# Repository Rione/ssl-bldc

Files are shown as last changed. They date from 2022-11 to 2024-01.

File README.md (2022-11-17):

# Ri-one BLDC Driver V1

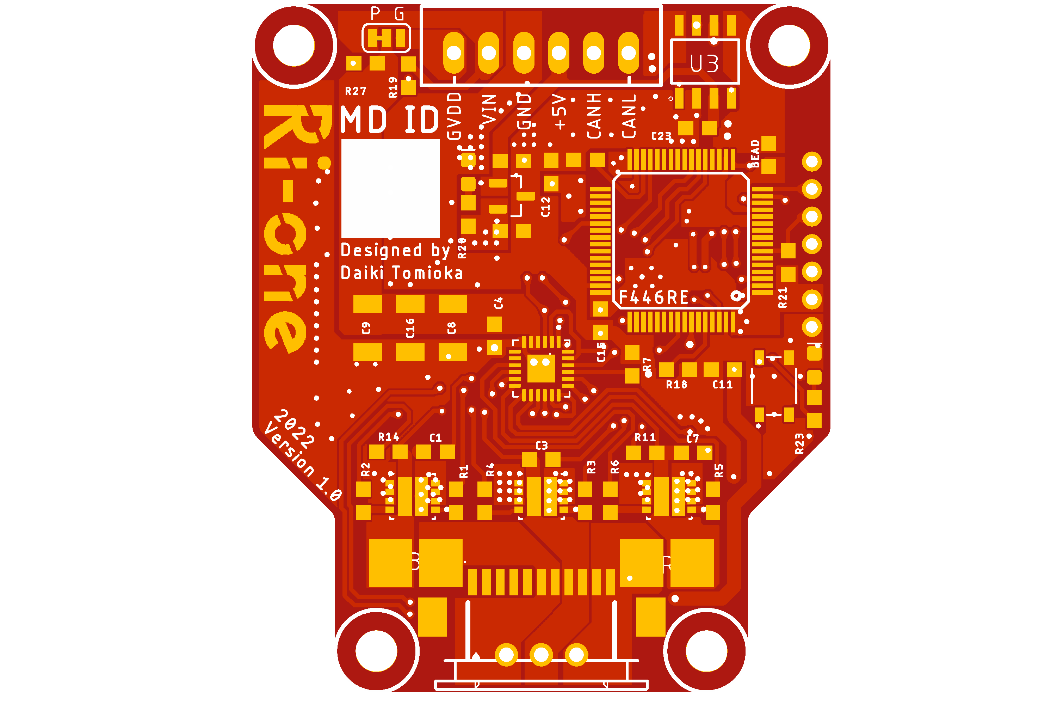
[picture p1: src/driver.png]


|  | IC |
| --- | --- |
| MOSFET | [SIZ254DT-T1-GE3](https://www.mouser.jp/ProductDetail/Vishay-Siliconix/SIZ254DT-T1-GE3?qs=pUKx8fyJudCKVjpWQE2G2A%3D%3D) |
| MCU | [STM32F446RET6](https://jp.rs-online.com/web/p/microcontrollers/1106621) |
| Gate Driver | [DVR8300DRGER](https://www.ti.com/product/DRV8300/part-details/DRV8300DRGER) |
| CAN Transceiver | [TJA1441AT](https://akizukidenshi.com/catalog/g/gI-17464/) |
| Shunt Resistor| 10mΩ | 
| 3.3V Regulator | [AP7333-33SAG](https://akizukidenshi.com/catalog/g/gI-11360/) |
| Motor | [EC 45 flat 30W](https://www.maxongroup.com/medias/sys_master/root/8846629470238/20-JP-285.pdf)|

---

初めて作ったモータドライバ基板です．
記事も書いたので，良かったら見てください．
[tomixrm 初のモタドラ設計！！ゲート抵抗を計算して求めてみた](https://tomixrm.vercel.app/2e7cb67096e143f2a43334a63c00d47e)

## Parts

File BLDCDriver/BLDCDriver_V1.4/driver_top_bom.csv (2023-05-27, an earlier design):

Comment | Designator | Footprint | LCSC Part #
 | R10 R13 | SMS-REF
 | SJ1 SJ2 | SJ
MLB1608-470(f) | BEAD | 603
CC0603KRX7R9BB104 | C10 C18 | 1608
CC0603KRX7R9BB104 | C1 C3 C4 C7 C11 C12 C15 C23 C25 | 603
CR-03FL7----1K | R20 | R0603
CR-03FL7----1K | R23 | 603
YC124-JR-071KL | R24 | YC124-JR-071KL
4.7uF | C14 | 603
10k | R27 | R0603
10k | R18 | R0603
RMS06JT103 | R19 | 603
RMS06JT103 | R21 | R0603
CL31A226KAHNNNE | C8 C9 C16 C24 | 1210
CR0603FA51R0G | R1 R2 R3 R4 R5 R6 | 603
50k | R7 | 603
AP7333-33SAG-7 | REG | SOT95P237X112-3N
STM32F446RE | NUCLEO_MAIN | STM32F446RET6
FFC12_11PIN_1MM | . | CON-SMT-FFCFPC_52207-1185
XL-3528RGBW-HM | U$1 | 3528LSEKJ3ZGKQBKS
MCP2562-E/SN | U3 | SOIC127P600X175-8N
DRV8300DRGER | U1 | QFN50P400X400X100-25N
SIZ240DT-T1-GE3 | Q2 Q3 Q4 | TRANS_SIZ240DT-T1-GE3
SKRPACE010 | S1 | SW_SKRPACE010
WHITE | D3 D6 | LED-0603

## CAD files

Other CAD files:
BLDCDriver/BLDCDriver_V1.4/drive.dxf

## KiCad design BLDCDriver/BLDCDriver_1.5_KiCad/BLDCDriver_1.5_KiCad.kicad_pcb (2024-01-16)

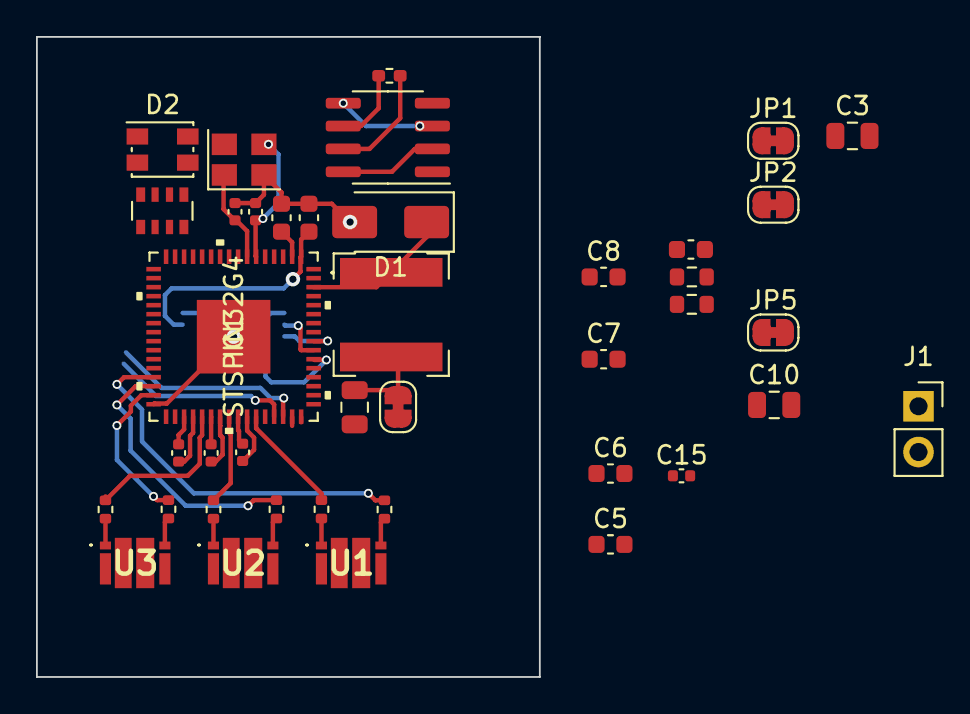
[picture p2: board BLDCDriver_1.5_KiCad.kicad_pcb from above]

Board: 2 copper layers, 27.9 x 35.6 mm, 41 parts (1 on the bottom side), 42 nets.

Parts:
C1, C2: 20p; C_0402_1005Metric
C3: 10uF; C_0805_2012Metric
C4, C6, C8, C9: 100nF; C_0603_1608Metric
C5, C7: 1uF; C_0603_1608Metric
C10: 220nF; C_0805_2012Metric
C11, C13, C14, C15: 1uF; C_0402_1005Metric
C12: N.M.; C_0603_1608Metric
C$1: 10uf 25v; C_0805_2012Metric
D1: SS210; D_SMA
D2: LED_RGBA; LED_Kingbright_AAA3528ESGCT
IC1: STSPIN32G4
J1: Conn_01x02_Male; PinSocket_1x02_P2.54mm_Vertical
JP1, JP2, JP3, JP5: Jumper_2_Bridged; SolderJumper-2_P1.3mm_Bridged_RoundedPad1.0x1.5mm
L1: 18uh; L_Bourns-SRN6028
R1: 22k; R_0603_1608Metric
R2: 10k; R_0603_1608Metric
R3: 120; R_0402_1005Metric_Pad0.72x0.64mm_HandSolder
R4, R5, R6, R7, R8, R9: 22k; R_0402_1005Metric
RN1: 1k; R_Array_Convex_4x0603
U1, U2, U3: SIZ254DTT1GE3
U4: MCP2562-E-SN; SOIC-8_3.9x4.9mm_P1.27mm
U5: AS5048A-HTSP-500; AS5048A_SOP65P640X120-14N
Y1: 12Mhz; Crystal_SMD_3225-4Pin_3.2x2.5mm

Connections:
BOOT1: C11.2, IC1.41 (BOOT1)
BOOT2: C13.2, IC1.38 (BOOT2)
BOOT3: C14.2, IC1.35 (BOOT3)
CANH: R3.1, U4.7 (CANH)
CANL: R3.2, U4.6 (CANL)
CAN_RD: IC1.47 (PA11), U4.4 (RXD)
CAN_TD: IC1.48 (PA12), U4.1 (TXD)
GHS1: IC1.43 (GHS1), R4.1
GHS2: IC1.40 (GHS2), R6.1
GHS3: IC1.37 (GHS3), R8.1
GLS1: IC1.29 (GLS1), R5.1
GLS2: IC1.30 (GLS2), R7.1
GLS3: IC1.31 (GLS3), R9.1
GND: C1.2, C2.2, C3.2, C4.2, C5.2, C6.2, C7.2, C8.2, C9.2, C10.2, C12.2, C15.1, C$1.2, D1.2 (A), IC1.32 (PGND), IC1.65 (VSS), R2.2, U1.5 (S), U2.5 (S), U3.5 (S), U4.2 (VSS), U4.8 (STBY), U5.13 (GND), Y1.2, Y1.4
unnamed: D2.3 (BK), RN1.2 (R2.1)
unnamed: D2.2 (GK), RN1.3 (R3.1)
unnamed: D2.1 (RK), RN1.4 (R4.1)
unnamed: C1.1, IC1.6 (PF0), Y1.3
unnamed: C2.1, IC1.7 (PF1), Y1.1
unnamed: C10.1, IC1.61 (VM), JP5.1 (A)
unnamed: C$1.1, JP3.1 (A), L1.2
unnamed: R4.2, U1.2 (G1)
unnamed: R5.2, U1.4 (G2)
unnamed: R6.2, U2.2 (G1)
unnamed: R7.2, U2.4 (G2)
unnamed: R8.2, U3.2 (G1)
unnamed: R9.2, U3.4 (G2)
OUT1: C11.1, IC1.42 (OUT1), U1.3 (O)
OUT2: C13.1, IC1.39 (OUT2), U2.3 (O)
OUT3: C14.1, IC1.36 (OUT3), U3.3 (O)
SCREF: C12.1, IC1.52 (SCREF), J1.2, R1.2, R2.1
SPI1_MISO: IC1.55 (PB4), U5.3 (MISO)
SPI1_MOSI: IC1.56 (PB5), U5.4 (MOSI)
SPI1_SCK: IC1.54 (PB3), U5.2 (CLK)
SW: D1.1 (K), IC1.62 (SW), L1.1
VBAT: C9.1, IC1.2 (VBAT), JP2.2 (B)
VCC: IC1.63 (VCC), JP1.1 (A), JP3.2 (B)
VD: U1.1 (D), U2.1 (D), U3.1 (D)
VDD: C3.1, C4.1, C15.2, D2.4 (A), IC1.1 (REG3V3/VDD), J1.1, JP2.1 (A), R1.1, U4.3 (VDD), U4.5 (Vio), U5.12 (VDD3V)
VDDA: C5.1, C6.1, IC1.27 (VDDA)
VREF+: C7.1, C8.1, IC1.26 (VREF+)
VREGIN: IC1.64 (REGIN), JP1.2 (B)

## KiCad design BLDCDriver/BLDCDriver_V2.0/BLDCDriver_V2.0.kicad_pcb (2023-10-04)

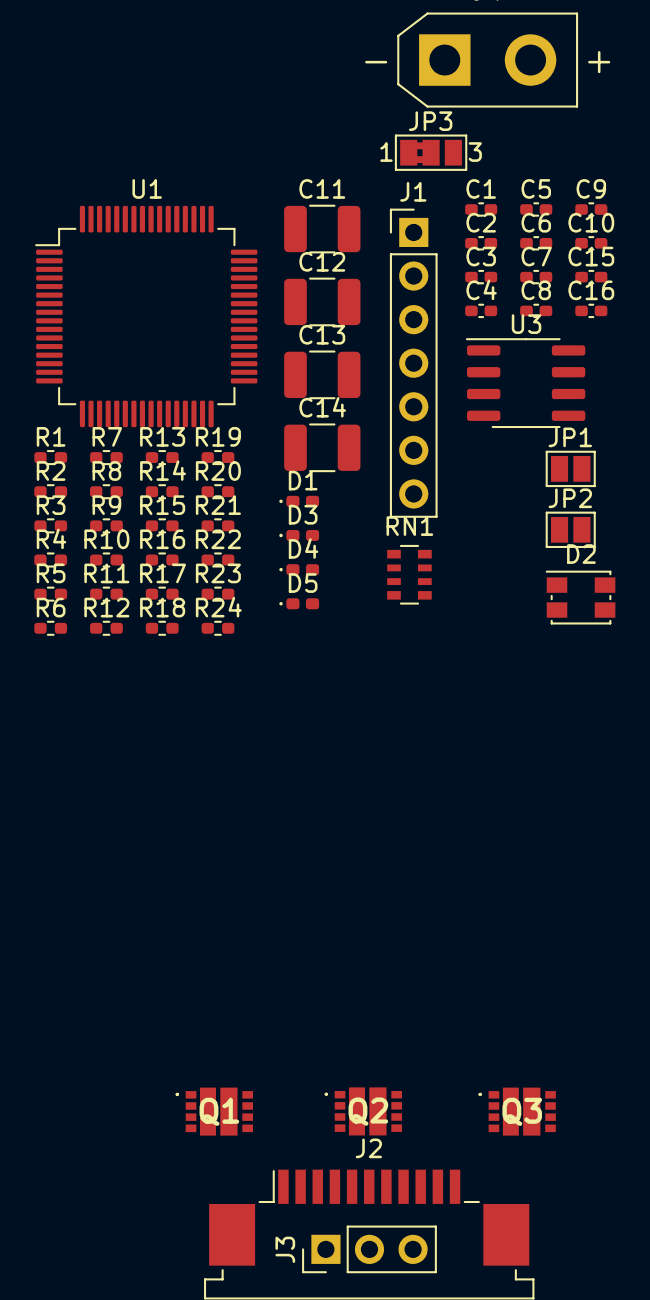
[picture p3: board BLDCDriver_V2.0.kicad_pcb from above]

Board: 2 copper layers, 58 parts (0 on the bottom side), 49 nets, no tracks yet.

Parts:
C1, C2, C3, C4, C5, C7, C8, C9, C10, C15, C16: 0.1u; C_0402_1005Metric_Pad0.74x0.62mm_HandSolder
C6: 4.7u; C_0402_1005Metric_Pad0.74x0.62mm_HandSolder
C11, C12, C13, C14: 22u; C_1210_3225Metric_Pad1.33x2.70mm_HandSolder
D1, D3, D4, D5: LED; LED_0402_1005Metric_Pad0.77x0.64mm_HandSolder
D2: LED_RGBA; LED_Kingbright_AAA3528ESGCT
J1: STLink; PinHeader_1x07_P2.54mm_Vertical
J2: Motor Out; TE_1-84952-1_1x11-1MP_P1.0mm_Horizontal
J3: Conn_01x03; PinHeader_1x03_P2.54mm_Vertical
J4: PowerIN; AMASS_XT30UPB-F_1x02_P5.0mm_Vertical
JP1, JP2: Jumper_2_Open; SolderJumper-2_P1.3mm_Open_Pad1.0x1.5mm
JP3: Jumper_3_Bridged12; SolderJumper-3_P1.3mm_Bridged2Bar12_Pad1.0x1.5mm_NumberLabe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
Q1, Q2, Q3: SIZ254DT-T1-GE3; SIZ254DTT1GE3
R1, R2, R15, R16: 10k; R_0402_1005Metric_Pad0.72x0.64mm_HandSolder
R3, R4, R5, R6, R7, R8, R9, R17: 1k; R_0402_1005Metric_Pad0.72x0.64mm_HandSolder
R10, R11, R12, R13: 33k; R_0402_1005Metric_Pad0.72x0.64mm_HandSolder
R14: 120; R_0402_1005Metric_Pad0.72x0.64mm_HandSolder
R18: 50k; R_0402_1005Metric_Pad0.72x0.64mm_HandSolder
R19, R20, R21, R22, R23, R24: 51; R_0402_1005Metric_Pad0.72x0.64mm_HandSolder
RN1: 1k; R_Array_Convex_4x0603
U1: (symbol "Device:C" (pin_numbers hide) (pin_names 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; LQFP-64_10x10mm_P0.5mm
U3: MCP2562-E-SN; SOIC-8_3.9x4.9mm_P1.27mm

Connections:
+3.3V: D2.4 (A), J1.1, U3.5 (Vio)
+3V3: C1.1, C2.1, C3.1, C4.1, C5.1, C7.1, C15.1, R1.1, R3.1
+5V: C16.1, U3.3 (VDD)
+BATT: C11.1, C12.1, C13.1, C14.1, J4.1, JP3.1 (A), Q1.2 (D), Q2.2 (D), Q3.2 (D), R15.1
CANH: R14.1, U3.7 (CANH)
CANL: R14.2, U3.6 (CANL)
CANRX: U1.62 (PB9), U3.4 (RXD)
CANTX: U1.61 (PB8), U3.1 (TXD)
GND: C6.2, C11.2, C12.2, C13.2, C14.2, C15.2, C16.2, D1.1 (K), D3.1 (K), D4.1 (K), D5.1 (K), J1.2, J2.MP (MountPin), J4.2, JP1.2 (B), JP2.2 (B), Q1.5 (S), Q2.5 (S), Q3.5 (S), R2.1, R10.2, R11.2, R18.2, U1.12 (VSSA), U1.18 (VSS), U1.31 (VSS), U1.47 (VSS), U1.63 (VSS), U3.2 (VSS), U3.8 (STBY)
LED: R17.1, U1.3 (PC14)
LED_B: RN1.7 (R2.2), U1.34 (PB13)
LED_G: RN1.6 (R3.2), U1.36 (PB15)
LED_R: RN1.5 (R4.2), U1.35 (PB14)
unnamed: C2.2, U1.19 (VDD)
unnamed: C3.2, U1.32 (VDD)
unnamed: C4.2, U1.48 (VDD)
unnamed: C5.2, U1.64 (VDD)
unnamed: D1.2 (A), R3.2
unnamed: D2.3 (BK), RN1.2 (R2.1)
unnamed: D2.2 (GK), RN1.3 (R3.1)
unnamed: D2.1 (RK), RN1.4 (R4.1)
unnamed: D3.2 (A), R15.2
unnamed: D4.2 (A), R16.2
unnamed: D5.2 (A), R17.2
unnamed: Q1.1 (G1), R19.2
unnamed: Q1.8 (G2), R20.2
unnamed: Q2.1 (G1), R21.2
unnamed: Q2.8 (G2), R22.2
unnamed: Q3.1 (G1), R23.2
unnamed: Q3.8 (G2), R24.2
unnamed: R2.2, U1.60 (BOOT0)
unnamed: R1.2, U1.7 (NRST)
unnamed: C1.2, U1.1 (VBAT)
unnamed: C6.1, U1.30 (VCAP_1)
unnamed: C7.2, U1.13 (VDDA)
unnamed: R6.2, R12.1
unnamed: R7.2, R10.1
unnamed: R8.2, R13.1
unnamed: R9.2, R11.1
U: C8.1, Q3.10 (O), R4.2, R6.1
UOut: J2.7, J2.8, J3.1, R4.1, R7.1
USBRX: J1.6, U1.17 (PA3)
V: C9.1, Q2.10 (O)
VDD: JP3.2 (C), JP3.3 (B), R16.1
VOut: J2.9, J2.10, J3.2
W: C10.1, Q1.10 (O), R5.2, R8.1
WOut: J2.11, J3.3, R5.1, R9.1
modeA: JP1.1 (A), U1.59 (PB7)
modeB: JP2.1 (A), U1.57 (PB5)

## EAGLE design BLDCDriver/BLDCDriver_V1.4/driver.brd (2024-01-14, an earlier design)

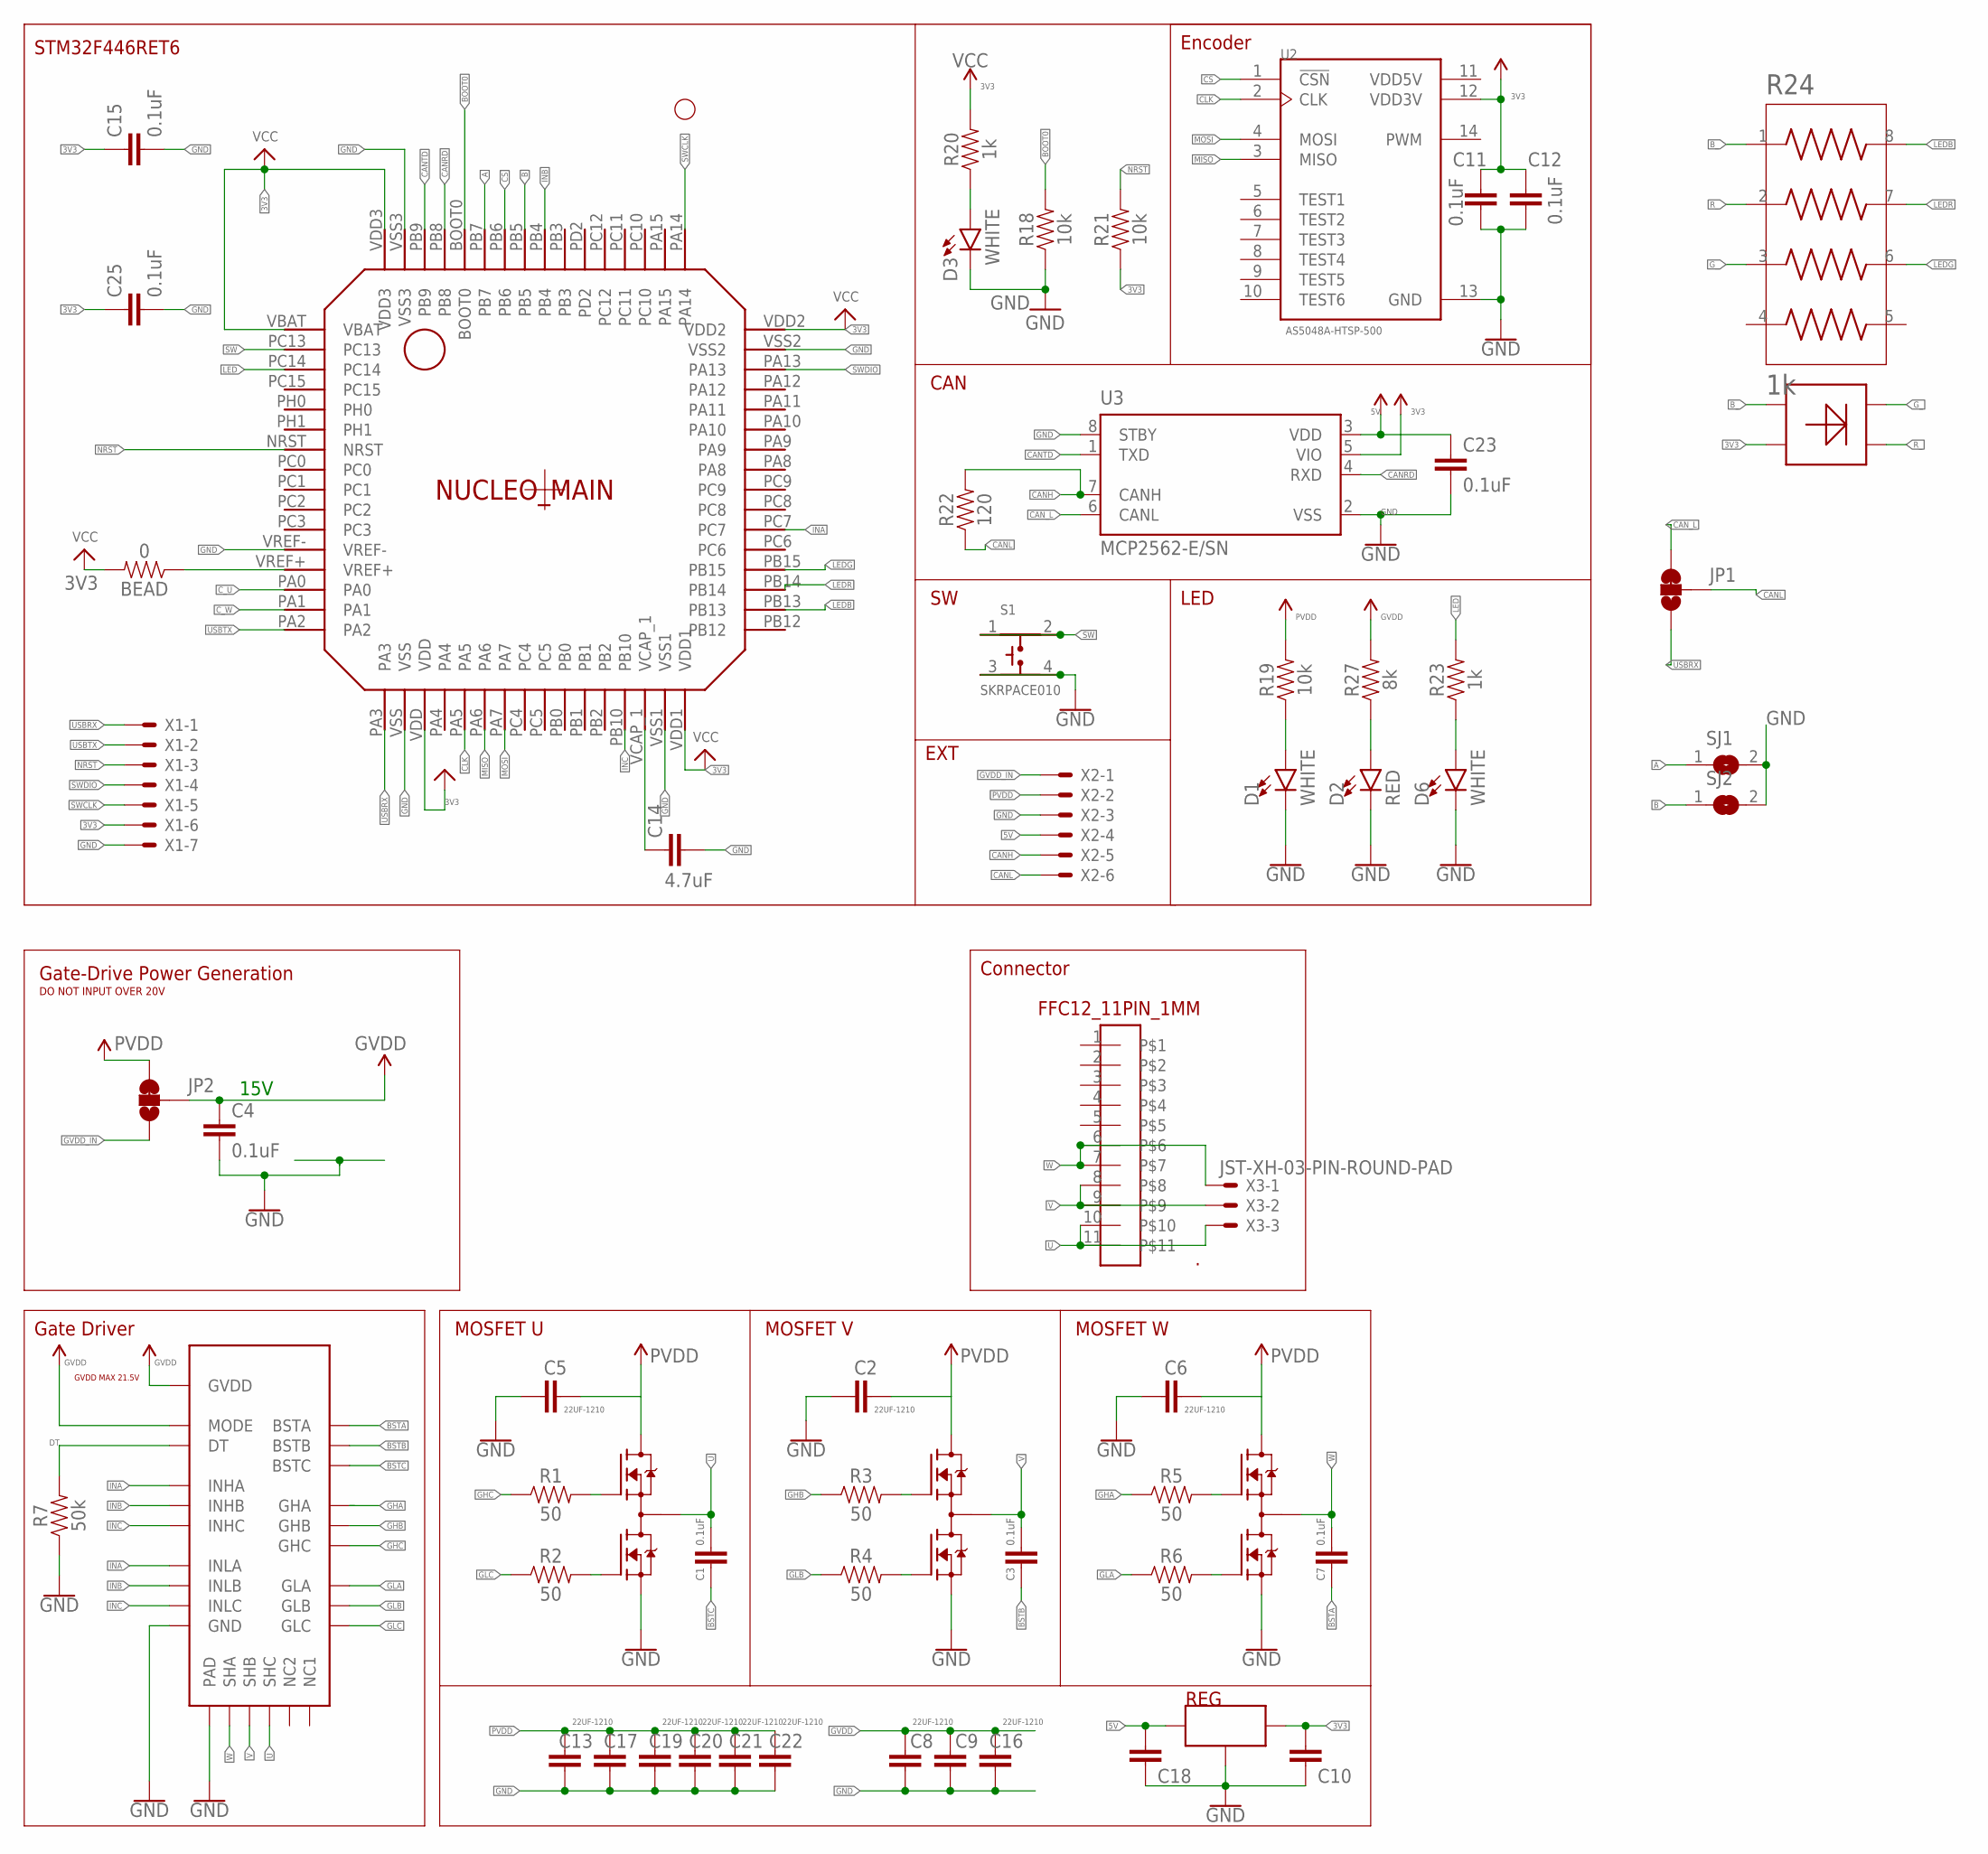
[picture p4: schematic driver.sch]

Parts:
.: FFC12_11PIN_1MM; CON-SMT-FFCFPC_52207-1185
BEAD: 0; 0603
C1, C3, C4, C7, C11, C12, C15, C23, C25: 0.1uF; 0603
C2, C5, C6, C8, C9, C13, C16, C17, C19, C20, C21, C22: 22UF-1210; 1210
C10, C18: 0.1UF; 1608
C14: 4.7uF; 0603
D1, D3, D6: WHITE; LED-0603
D2: RED; LED-0603
JP1, JP2: JUMPER-SMT_3_1-NC_TRACE_SILK; SMT-JUMPER_3_1-NC_TRACE_SILK
NUCLEO_MAIN: F446RET6; STM32F446RET6
Q2, Q3, Q4: SIZ240DT-T1-GE3; TRANS_SIZ240DT-T1-GE3
R1, R2, R3, R4, R5, R6: 50; 0603
R7: 50k; 0603
R18, R21: 10k; R0603
R19: 10k; 0603
R20: 1k; R0603
R22: 120; 0603
R23: 1k; 0603
R24: 1k; RESCAXS50P200X100X45-8N
R27: 8k; 0603
REG: AP7333; SOT95P237X112-3N
S1: SKRPACE010; SW_SKRPACE010
SJ1, SJ2: SJ
U1: QFN50P400X400X100-25NDRV8300DRGER; QFN50P400X400X100-25N
U2: AS5048A-HTSP-500; SOP65P640X120-14N
U3: MCP2562-E/SN; SOIC127P600X175-8N
U$1: LED; LED_AAA3528LSEKJ3ZGKQBKS
X1: JST-XH-07-PIN-ROUND-PAD; JST-XH-07-PACKAGE-ROUND-PAD
X2: JST-XH-06-PIN-LONG-PAD; JST-XH-06-PACKAGE-LONG-PAD
X3: JST-XH-03-PIN-ROUND-PAD; JST-XH-03-PACKAGE-ROUND-PAD

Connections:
3V3: BEAD.2, C10.1, C11.1, C12.1, C15.1, C25.1, NUCLEO_MAIN.VBAT, NUCLEO_MAIN.VDD, NUCLEO_MAIN.VDD1, NUCLEO_MAIN.VDD2, NUCLEO_MAIN.VDD3, R20.2, R21.1, REG.2 (OUT), U2.12 (VDD3V), U3.5 (VIO), U$1.4 (GND), X1.6
5V: C18.1, C23.1, REG.1 (IN), U3.3 (VDD), X2.4
A: NUCLEO_MAIN.PB7, SJ1.1
B: NUCLEO_MAIN.PB5, SJ2.1
BOOT0: NUCLEO_MAIN.BOOT0, R18.2
BSTA: C7.1, U1.BSTA
BSTB: C3.1, U1.BSTB
BSTC: C1.1, U1.BSTC
B_: R24.1, U$1.1 (B)
CANH: R22.2, U3.7 (CANH), X2.5
CANL: JP1.2, R22.1, X2.6
CANRD: NUCLEO_MAIN.PB8, U3.4 (RXD)
CANTD: NUCLEO_MAIN.PB9, U3.1 (TXD)
CAN_L: JP1.3, U3.6 (CANL)
CLK: NUCLEO_MAIN.PA5, U2.2 (CLK)
CS: NUCLEO_MAIN.PB6, U2.1 (!CSN)
C_U: NUCLEO_MAIN.PA0
C_W: NUCLEO_MAIN.PA1
DT: R7.2, U1.DT
GHA: R5.1, U1.GHA
GHB: R3.1, U1.GHB
GHC: R1.1, U1.GHC
GLA: R6.1, U1.GLA
GLB: R4.1, U1.GLB
GLC: R2.1, U1.GLC
GND: C2.1, C4.2, C5.1, C6.1, C8.1, C9.1, C10.2, C11.2, C12.2, C13.1, C14.2, C15.2, C16.1, C17.1, C18.2, C19.1, C20.1, C21.1, C22.1, C23.2, C25.2, D1.C, D2.C, D3.C, D6.C, NUCLEO_MAIN.VREF-, NUCLEO_MAIN.VSS, NUCLEO_MAIN.VSS1, NUCLEO_MAIN.VSS2, NUCLEO_MAIN.VSS3, Q2.5 (S2), Q2.6 (S2), Q2.7 (S2), Q3.5 (S2), Q3.6 (S2), Q3.7 (S2), Q4.5 (S2), Q4.6 (S2), Q4.7 (S2), R7.1, R18.1, REG.3 (GND), S1.3, S1.4, SJ1.2, SJ2.2, U1.GND, U1.PAD, U2.13 (GND), U3.2 (VSS), U3.8 (STBY), X1.7, X2.3
GVDD: C4.1, C8.2, C9.2, C16.2, JP2.2, R27.2, U1.GVDD, U1.MODE
GVDD_IN: JP2.1, X2.1
G_: R24.3, U$1.2 (G)
HA: Q4.1 (G1), R5.2
HB: Q3.1 (G1), R3.2
HC: Q2.1 (G1), R1.2
INA: NUCLEO_MAIN.PC7, U1.INHA, U1.INLA
INB: NUCLEO_MAIN.PB4, U1.INHB, U1.INLB
INC: NUCLEO_MAIN.PB10, U1.INHC, U1.INLC
L: D3.A, R20.1
LA: Q4.8 (G2), R6.2
LB: Q3.8 (G2), R4.2
LC: Q2.8 (G2), R2.2
LED: NUCLEO_MAIN.PC14, R23.2
LEDB: NUCLEO_MAIN.PB13, R24.8
LEDG: NUCLEO_MAIN.PB15, R24.6
LEDR: NUCLEO_MAIN.PB14, R24.7
MISO: NUCLEO_MAIN.PA6, U2.3 (MISO)
MOSI: NUCLEO_MAIN.PA7, U2.4 (MOSI)
unnamed: D1.A, R19.1
unnamed: D2.A, R27.1
unnamed: D6.A, R23.1
NRST: NUCLEO_MAIN.NRST, R21.2, X1.3
PVDD: C2.2, C5.2, C6.2, C13.2, C17.2, C19.2, C20.2, C21.2, C22.2, JP2.3, Q2.2 (D1), Q2.3 (D1), Q2.4 (D1), Q2.10 (D1), Q3.2 (D1), Q3.3 (D1), Q3.4 (D1), Q3.10 (D1), Q4.2 (D1), Q4.3 (D1), Q4.4 (D1), Q4.10 (D1), R19.2, X2.2
R_: R24.2, U$1.3 (R)
SW: NUCLEO_MAIN.PC13, S1.1, S1.2
SWCLK: NUCLEO_MAIN.PA14, X1.5
SWDIO: NUCLEO_MAIN.PA13, X1.4
U: ..10, ..11, C1.2, Q2.9 (S1/D2), U1.SHC, X3.3
USBRX: JP1.1, NUCLEO_MAIN.PA3, X1.1
USBTX: NUCLEO_MAIN.PA2, X1.2
V: ..8, ..9, C3.2, Q3.9 (S1/D2), U1.SHB, X3.2
VCAP: C14.1, NUCLEO_MAIN.VCAP_1
VDD5V: U2.11 (VDD5V)
VDDA: BEAD.1, NUCLEO_MAIN.VREF+
W: ..6, ..7, C7.2, Q4.9 (S1/D2), U1.SHA, X3.1

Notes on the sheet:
GVDD MAX 21.5V
15V
Gate-Drive Power Generation
Gate Driver
MOSFET U
Connector
Encoder
STM32F446RET6
MOSFET V
MOSFET W
DO NOT INPUT OVER 20V
CAN
LED
EXT

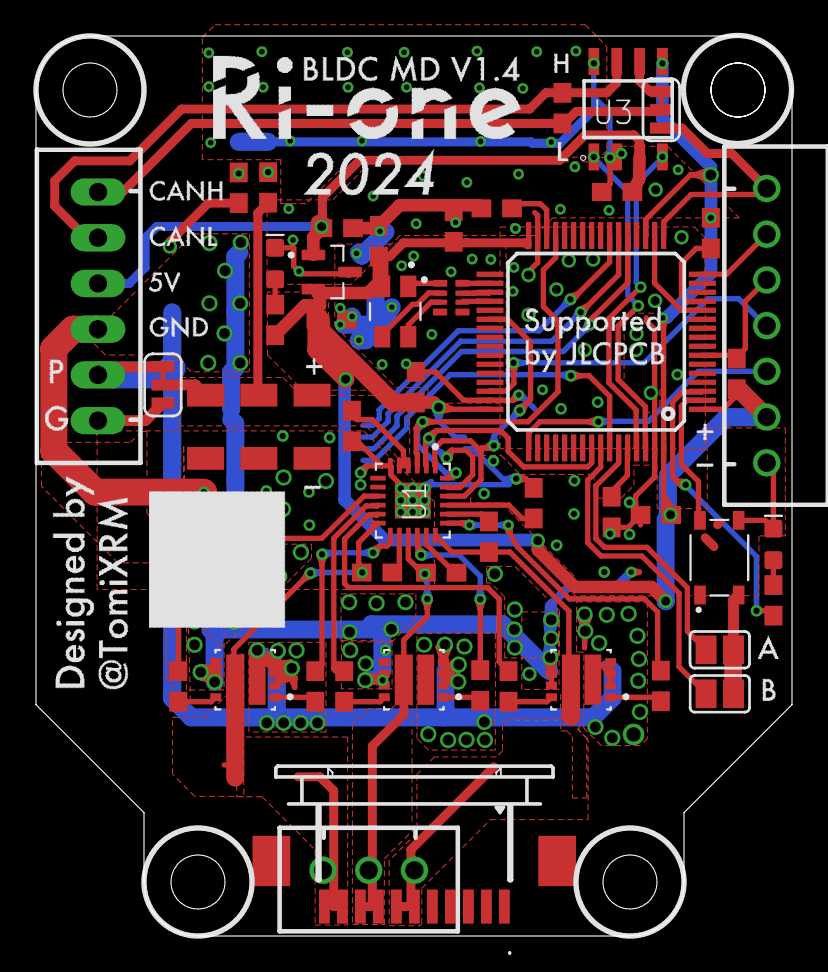
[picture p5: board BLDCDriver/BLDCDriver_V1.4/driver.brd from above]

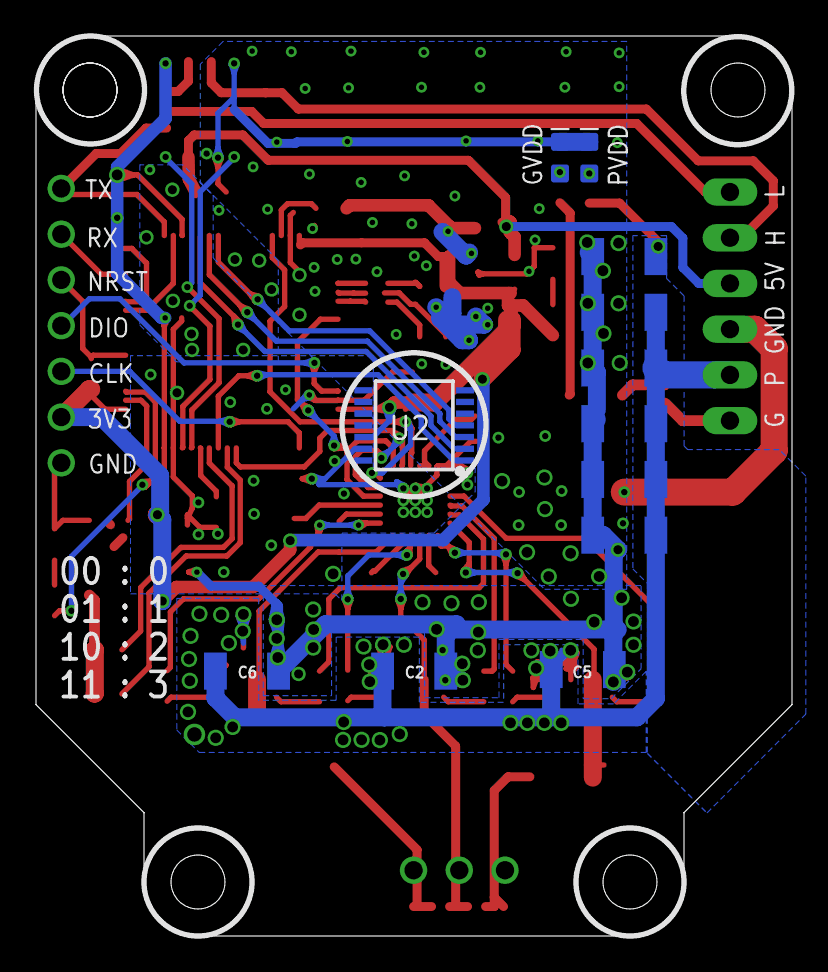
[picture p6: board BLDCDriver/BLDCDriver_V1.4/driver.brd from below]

Board: 2 copper layers, 42.0 x 50.0 mm, 62 parts (12 on the bottom side), 59 nets.

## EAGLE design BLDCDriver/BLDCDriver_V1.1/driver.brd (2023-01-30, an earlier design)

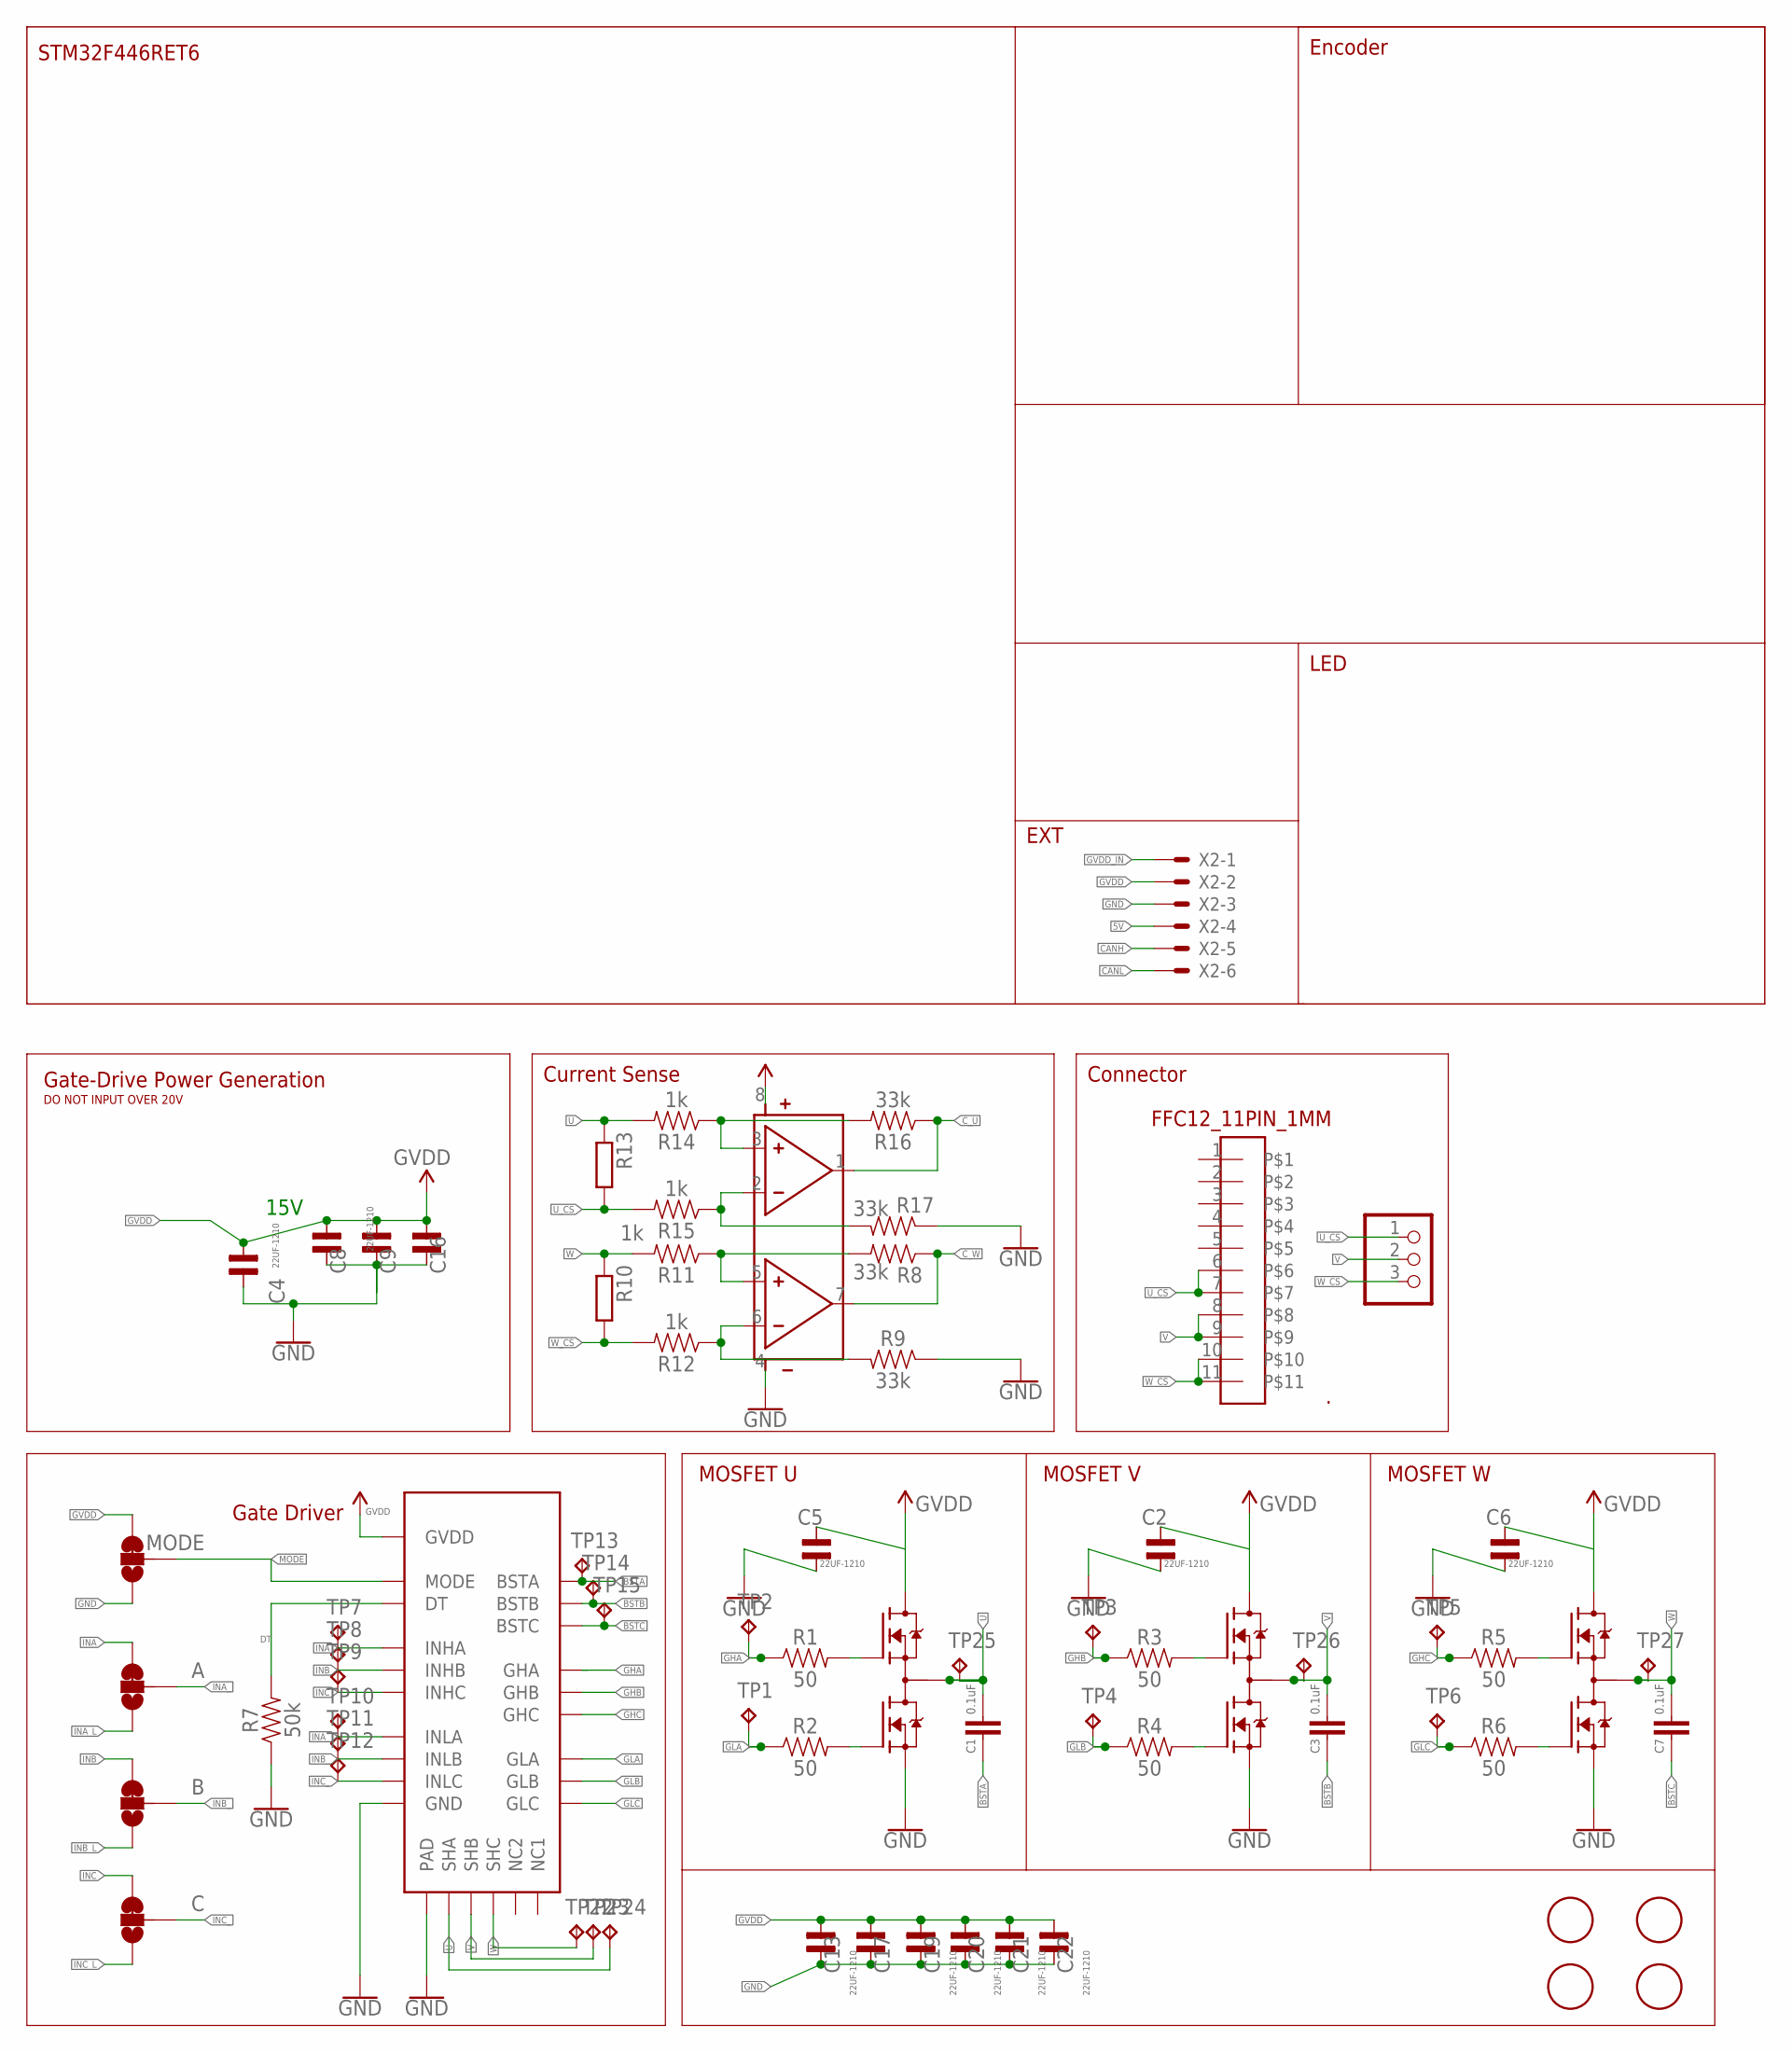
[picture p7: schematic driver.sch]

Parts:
.: FFC12_11PIN_1MM; CON-SMT-FFCFPC_52207-1185
A: JUMPER-SMT_3_1-NC_TRACE_SILK; SMT-JUMPER_3_1-NC_TRACE_SILK
B: JUMPER-SMT_3_1-NC_TRACE_SILK; SMT-JUMPER_3_1-NC_TRACE_SILK
C: JUMPER-SMT_3_1-NC_TRACE_SILK; SMT-JUMPER_3_1-NC_TRACE_SILK
C1, C3, C7: 0.1uF; 0603
C2, C5, C6, C8, C9, C13, C16, C17, C19, C20, C21, C22: 22UF-1210; 0805
C4: 0.1uF; 0805
JP3: PINHD-1X3CB; 1X03-CLEANBIG
MODE: JUMPER-SMT_3_1-NC_TRACE_SILK; SMT-JUMPER_3_1-NC_TRACE_SILK
Q2, Q3, Q4: SIZ240DT-T1-GE3; TRANS_SIZ240DT-T1-GE3
R1, R2, R3, R4, R5, R6: 50; 0603
R7: 50k; 0603
R8, R9, R16, R17: 33k; 0603
R10, R13: SMS-REF
R11, R12, R14, R15: 1k; 0603
TP1, TP2, TP3, TP4, TP5, TP6, TP7, TP8, TP9, TP10, TP11, TP12, TP13, TP14, TP15, TP22, TP23, TP24, TP25, TP26, TP27: TPPAD1-13; P1-13
U1: QFN50P400X400X100-25NDRV8300DRGER; QFN50P400X400X100-25N
U4: SOP80P620X125-8N
U$1, U$3, U$4, U$5: PIN; 3MM
X2: JST-XH-06-PIN-LONG-PAD; JST-XH-06-PACKAGE-LONG-PAD

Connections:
3V3: U4.8 (VDD)
5V: X2.4
BSTA: C1.1, TP13.TP, U1.BSTA
BSTB: C3.1, TP14.TP, U1.BSTB
BSTC: C7.1, TP15.TP, U1.BSTC
CANH: X2.5
CANL: X2.6
C_U: R16.1, U4.1 (O1)
C_W: R8.1, U4.7 (O2)
DT: R7.2, U1.DT
GHA: R1.1, TP2.TP, U1.GHA
GHB: R3.1, TP3.TP, U1.GHB
GHC: R5.1, TP5.TP, U1.GHC
GLA: R2.1, TP1.TP, U1.GLA
GLB: R4.1, TP4.TP, U1.GLB
GLC: R6.1, TP6.TP, U1.GLC
GND: C2.1, C4.2, C5.1, C6.1, C8.1, C9.1, C13.1, C16.1, C17.1, C19.1, C20.1, C21.1, C22.1, MODE.1, Q2.5 (S2), Q2.6 (S2), Q2.7 (S2), Q3.5 (S2), Q3.6 (S2), Q3.7 (S2), Q4.5 (S2), Q4.6 (S2), Q4.7 (S2), R7.1, R9.1, R17.1, U1.GND, U1.PAD, U4.4 (GND), X2.3
GVDD: C2.2, C4.1, C5.2, C6.2, C8.2, C9.2, C13.2, C16.2, C17.2, C19.2, C20.2, C21.2, C22.2, MODE.3, Q2.2 (D1), Q2.3 (D1), Q2.4 (D1), Q2.10 (D1), Q3.2 (D1), Q3.3 (D1), Q3.4 (D1), Q3.10 (D1), Q4.2 (D1), Q4.3 (D1), Q4.4 (D1), Q4.10 (D1), U1.GVDD, X2.2
GVDD_IN: X2.1
HA: Q2.1 (G1), R1.2
HB: Q3.1 (G1), R3.2
HC: Q4.1 (G1), R5.2
INA: A.3, TP7.TP, U1.INHA
INA_: A.2, TP10.TP, U1.INLA
INA_L: A.1
INB: B.3, TP8.TP, U1.INHB
INB_: B.2, TP11.TP, U1.INLB
INB_L: B.1
INC: C.3, TP9.TP, U1.INHC
INC_: C.2, TP12.TP, U1.INLC
INC_L: C.1
LA: Q2.8 (G2), R2.2
LB: Q3.8 (G2), R4.2
LC: Q4.8 (G2), R6.2
MODE: MODE.2, U1.MODE
unnamed: R8.2, R11.1, U4.5 (P2)
unnamed: R9.2, R12.1, U4.6 (M2)
unnamed: R14.1, R16.2, U4.3 (P1)
unnamed: R15.1, R17.2, U4.2 (M1)
U: C1.2, Q2.9 (S1/D2), R13.2, R14.2, TP24.TP, TP25.TP, U1.SHA
U_CS: ..6, ..7, JP3.1, R13.1, R15.2
V: ..8, ..9, C3.2, JP3.2, Q3.9 (S1/D2), TP23.TP, TP26.TP, U1.SHB
W: C7.2, Q4.9 (S1/D2), R10.2, R11.2, TP22.TP, TP27.TP, U1.SHC
W_CS: ..10, ..11, JP3.3, R10.1, R12.2

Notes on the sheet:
15V
Gate-Drive Power Generation
Gate Driver
MOSFET U
Current Sense
Connector
Encoder
STM32F446RET6
MOSFET V
MOSFET W
DO NOT INPUT OVER 20V
LED
EXT

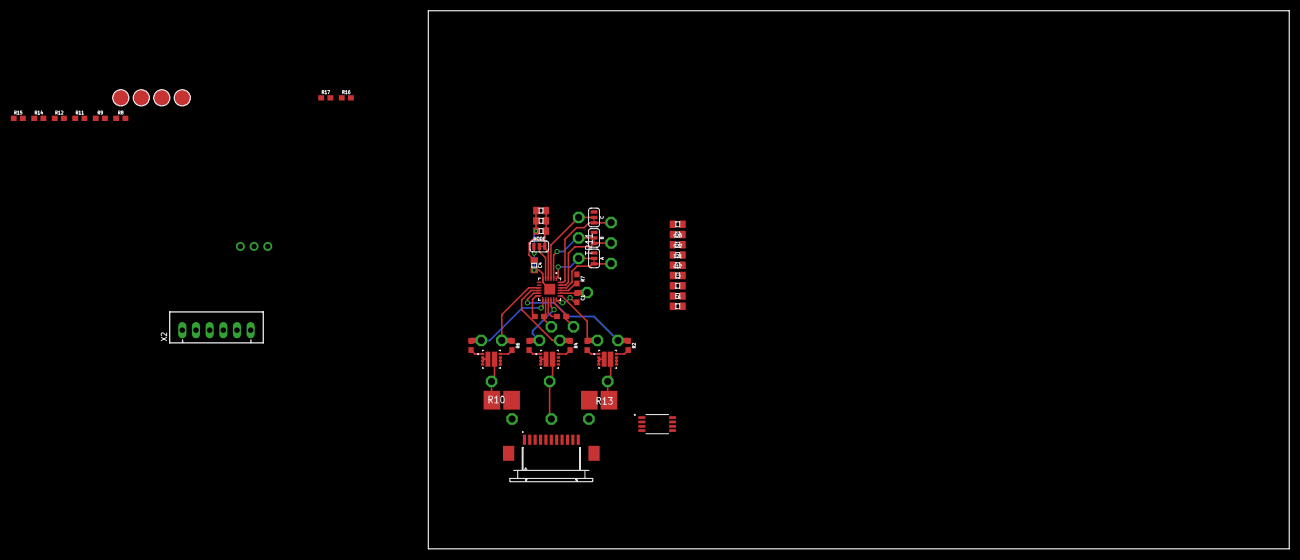
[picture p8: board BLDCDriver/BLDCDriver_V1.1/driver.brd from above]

Board: 2 copper layers, 160.0 x 100.0 mm, 70 parts (0 on the bottom side), 36 nets.

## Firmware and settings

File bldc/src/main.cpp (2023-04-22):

/**
 *
 * Velocity motion control example
 * Steps:
 * 1) Configure the motor and magnetic sensor
 * 2) Run the code
 * 3) Set the target velocity (in radians per second) from serial terminal
 *
 *
 * By using the serial terminal set the velocity value you want to motor to obtain
 *
 */
#include <SimpleFOC.h>

// magnetic sensor instance - SPI
MagneticSensorSPI sensor = MagneticSensorSPI(AS5147_SPI, 10);
// magnetic sensor instance - MagneticSensorI2C
// MagneticSensorI2C sensor = MagneticSensorI2C(AS5600_I2C);
// MagneticSensorAnalog sensor = MagneticSensorAnalog(A1, 14, 1020);

// BLDC motor & driver instance
BLDCMotor motor = BLDCMotor(8);
BLDCDriver3PWM driver = BLDCDriver3PWM(9, 5, 6);

// velocity set point variable
float target_velocity = 50;
// instantiate the commander
Commander command = Commander(Serial);
void doTarget(char *cmd) { command.scalar(&target_velocity, cmd); }

void setup() {

    // initialise magnetic sensor hardware
    sensor.init();
    // link the motor to the sensor
    motor.linkSensor(&sensor);

    // driver config
    // power supply voltage [V]
    driver.voltage_power_supply = 15;
    driver.init();
    // link the motor and the driver
    motor.linkDriver(&driver);

    // set motion control loop to be used
    motor.controller = MotionControlType::velocity;

    // contoller configuration
    // default parameters in defaults.h

    // velocity PI controller parameters
    motor.PID_velocity.P = 0.2;
    motor.PID_velocity.I = 1;
    motor.PID_velocity.D = 0.000001;
    // default voltage_power_supply
    motor.voltage_limit = 5;
    // jerk control using voltage voltage ramp
    // default value is 300 volts per sec  ~ 0.3V per millisecond
    motor.PID_velocity.output_ramp = 1000;

    // velocity low pass filtering
    // default 5ms - try different values to see what is the best.
    // the lower the less filtered
    motor.LPF_velocity.Tf = 0.01f;

    // use monitoring with serial
    Serial.begin(2000000);
    // comment out if not needed
    motor.useMonitoring(Serial);

    // initialize motor
    motor.init();
    // align sensor and start FOC
    motor.initFOC();

    // add target command T
    command.add('T', doTarget, "target voltage");

    Serial.println(F("Motor ready."));
    Serial.println(F("Set the target velocity using serial terminal:"));
    _delay(1000);
}

void loop() {
    // main FOC algorithm function
    // the faster you run this function the better
    // Arduino UNO loop  ~1kHz
    // Bluepill loop ~10kHz
    motor.loopFOC();

    // Motion control function
    // velocity, position or voltage (defined in motor.controller)
    // this function can be run at much lower frequency than loopFOC() function
    // You can also use motor.move() and set the motor.target in the code
    motor.move(target_velocity);

    // function intended to be used with serial plotter to monitor motor variables
    // significantly slowing the execution down!!!!
    // motor.monitor();

    // user communicationT

    command.run();
}

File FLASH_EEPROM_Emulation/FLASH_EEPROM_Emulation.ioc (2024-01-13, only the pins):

Mcu.UserName=STM32F446RETx
PA13.GPIO_Label=TMS
PA13.Signal=SYS_JTMS-SWDIO
PA14.GPIO_Label=TCK
PA14.Signal=SYS_JTCK-SWCLK
PA2.GPIO_Label=USART_TX
PA2.Signal=USART2_TX
PA3.GPIO_Label=USART_RX
PA3.Signal=USART2_RX
PA5.Signal=SPI1_SCK
PA6.Signal=SPI1_MISO
PA7.Signal=SPI1_MOSI
PB10.GPIO_Label=PWM1_C
PB10.Signal=S_TIM2_CH3
PB13.GPIO_Label=led_blue
PB13.Signal=GPIO_Output
PB14.GPIO_Label=led_red
PB14.Signal=GPIO_Output
PB15.GPIO_Label=led_green
PB15.Signal=GPIO_Output
PB3.GPIO_Label=SWO
PB3.Signal=SYS_JTDO-SWO
PB4.GPIO_Label=PWM1_B
PB4.Signal=S_TIM3_CH1
PB5.GPIO_Label=sw_B
PB5.Signal=GPIO_Input
PB6.GPIO_Label=CS1
PB6.Signal=GPIO_Output
PB7.GPIO_Label=sw_A
PB7.Signal=GPIO_Input
PB8.Signal=CAN1_RX
PB9.Signal=CAN1_TX
PC13.GPIO_Label=B1 [Blue PushButton]
PC13.Signal=GPXTI13
PC14-OSC32_IN.GPIO_Label=led_alive
PC14-OSC32_IN.Signal=GPIO_Output
PC7.GPIO_Label=PWM1_A
PC7.Signal=S_TIM3_CH2

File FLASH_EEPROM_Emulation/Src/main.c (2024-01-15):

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
/* Includes ------------------------------------------------------------------*/
#include "main.h"
#include "can.h"
#include "dma.h"
#include "spi.h"
#include "tim.h"
#include "usart.h"
#include "gpio.h"

/* USER CODE BEGIN Includes */
#include "./App/app.hpp"
/* USER CODE END Includes */

/* USER CODE BEGIN PTD */
#ifdef __GNUC__
#define PUTCHAR_PROTOTYPE int __io_putchar(int ch)
#define GETCHAR_PROTOTYPE int __io_getchar(void)
#else
#define PUTCHAR_PROTOTYPE int fputc(int ch, FILE *f)
#define GETCHAR_PROTOTYPE int f getc(FILE *f)
#endif
/* USER CODE END PTD */


void SystemClock_Config(void);
/**
 * @brief  The application entry point.
 * @retval int
 */
int main(void) {
    /* USER CODE BEGIN 1 */
    setbuf(stdout, NULL);
    /* USER CODE END 1 */

    /* MCU Configuration--------------------------------------------------------*/

    /* Reset of all peripherals, Initializes the Flash interface and the Systick. */
    HAL_Init();

    /* Configure the system clock */
    SystemClock_Config();

    /* Initialize all configured peripherals */
    MX_GPIO_Init();
    MX_DMA_Init();
    MX_USART2_UART_Init();
    MX_SPI1_Init();
    MX_CAN1_Init();
    MX_TIM1_Init();
    MX_TIM3_Init();
    MX_TIM2_Init();
    /* Infinite loop */
    /* USER CODE BEGIN WHILE */
    while (1) {
        main_app();
        /* USER CODE END WHILE */

        /* USER CODE BEGIN 3 */
    }
    /* USER CODE END 3 */
}

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
/* USER CODE BEGIN 4 */
int _write(int file, char *ptr, int len) {
    HAL_UART_Transmit(&huart2, (uint8_t *)ptr, len, 10);
    return len;
}

void __io_putchar(uint8_t ch) {
    HAL_UART_Transmit(&huart2, &ch, 1, 0xFFFFFFFF);
}

int __io_getchar(void) {
    uint8_t rxBuf;
    while (HAL_UART_Receive(&huart2, &rxBuf, 1, 0xFFFFFFFF) != HAL_OK)
        ;
    return (rxBuf);
}
/* USER CODE END 4 */
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


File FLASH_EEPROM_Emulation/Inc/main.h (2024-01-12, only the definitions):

#define B1_Pin GPIO_PIN_13
#define B1_GPIO_Port GPIOC
#define led_alive_Pin GPIO_PIN_14
#define led_alive_GPIO_Port GPIOC
#define USART_TX_Pin GPIO_PIN_2
#define USART_TX_GPIO_Port GPIOA
#define USART_RX_Pin GPIO_PIN_3
#define USART_RX_GPIO_Port GPIOA
#define PWM1_C_Pin GPIO_PIN_10
#define PWM1_C_GPIO_Port GPIOB
#define led_blue_Pin GPIO_PIN_13
#define led_blue_GPIO_Port GPIOB
#define led_red_Pin GPIO_PIN_14
#define led_red_GPIO_Port GPIOB
#define led_green_Pin GPIO_PIN_15
#define led_green_GPIO_Port GPIOB
#define PWM1_A_Pin GPIO_PIN_7
#define PWM1_A_GPIO_Port GPIOC
#define TMS_Pin GPIO_PIN_13
#define TMS_GPIO_Port GPIOA
#define TCK_Pin GPIO_PIN_14
#define TCK_GPIO_Port GPIOA
#define SWO_Pin GPIO_PIN_3
#define SWO_GPIO_Port GPIOB
#define PWM1_B_Pin GPIO_PIN_4
#define PWM1_B_GPIO_Port GPIOB
#define sw_B_Pin GPIO_PIN_5
#define sw_B_GPIO_Port GPIOB
#define CS1_Pin GPIO_PIN_6
#define CS1_GPIO_Port GPIOB
#define sw_A_Pin GPIO_PIN_7
#define sw_A_GPIO_Port GPIOB

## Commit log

2022-10-15 set limitation of velocity at 100
2022-10-15 achieve to turn a motor on STM32
    lib_archive = falseをするとplatoformIOのSTM32duinoがちゃんと動いてくれる
2022-10-16 add schematic
    [driver.sch]
2022-10-18 add MOSFETs on driver schematic
    [driver.sch]
2022-10-19 ゲート抵抗の計算をするためにグラフ描いた
2022-11-04 ゲートドライバを50Ωに決定した
    詳しくは https://www.notion.so/rionessl/MOSFET-c3f0bc53d559421c83d572cacaf1d697#0553bd1ca6b7412ab2f7f6d7e1a45fa8
    [driver.sch]
2022-11-05 CurrentSenseを追加した
    [driver.brd, driver.sch]
2022-11-05 STM32と磁気エンコーダを追加した
    [driver.brd, driver.sch]
2022-11-05 somefix
    # ==== Emojis ====
    # ✨ :sparkles: Add new feature
    # ✅ :white_check_mark: Update existing feature (not bug)
    # ⚠️ :warning: Fix bug/error
    # 🔥 :fire: Remove files or features
    # ✏️ :pencil2: Fix typos
    # 📝 :memo: Update documentation
    # ♻️ :recycle: Dependencies update
    # 🐧 :penguin: Improved the Linux
    # 🍎 :apple: Improved the macOS
    # 🔖 :bookmark: Add new library
    # 🎉 :tada: Initial commit
    # ==== Format ====
    # :emoji: Subject
    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
    [driver.brd, driver.sch]
2022-11-06 自分、泣いていいすか
    [driver.brd, driver.sch]
2022-11-06 救いはないんですか〜？
    #
    # Commit body...
    # ==== Messages ====
    # 新規(ファイル)機能追加: Add
    # 機能修正、既存機能追加（バグではない): Update
    # リファクタリング: Clean
    # ファイル名変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
    [driver.brd, driver.sch]
2022-11-07 ちょっと頑張った
    # ファイル名変更:
    #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
    [driver.brd, driver.sch]
2022-11-08 いい感じの配置アイディアが降ってきた
    - 裏側にも実装する
    - 20V非対応にする(GVDD別供給にも対応)
    [driver.brd]
2022-11-08 モータ固定台のシルク入れた
    # ファイル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
    [drive.dxf, driver.brd, driver.sch]
2022-11-08 シャント抵抗を裏側にした。GVDD消した
    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
    [driver.brd, driver.sch]
2022-11-08 気合いが足りない。
    # 削除など: Remo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
    [driver.brd]
2022-11-09 CANに対応していき
    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
    [driver.brd, driver.sch]
2022-11-09 ちょっと希望が見えた
    [drive.dxf, driver.brd]
2022-11-09 希望が見えてきた
    [driver.brd, driver.sch]
2022-11-09 配線頑張った
    [driver.brd, driver.sch]
2022-11-09 𝐏𝐎𝐖𝐄𝐑した
    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
    [driver.brd]
2022-11-09 FETにビア通した
    # 削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
    [driver.brd, driver.sch]
2022-11-09 配線1からやり直し
    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
    [driver.brd]
2022-11-09 配置プロった
    - コンデンサを追加した。
    - 電流センシングの相をVからWに変えた
    - パワーラインから配線はじめた
    [driver.brd, driver.sch]
2022-11-09 いい感じ🦀
    # 削除な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
    [driver.brd, driver.sch]
2022-11-09 ゲートドライバ周りの配線全部終わらせた
    # リファクタリング: Cl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
    [driver.brd, driver.sch]
2022-11-10 CANの配線をした
    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
    [driver.brd, driver.sch]
2022-11-10 🔥完全体
    1日寝かせる
    [driver.brd]
2022-11-10 電源ラインのパワみを増やした
    # ファイ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
    [driver.brd]
2022-11-11 DXFを復元した
    [drive.dxf]
2022-11-11 ⚡️電源周りの配線パワみ増した
    [driver.brd]
2022-11-11 CANトランシーバーの近くにコンデンサつけた
    [driver.brd, driver.sch]
2022-11-11 ボードをパネライズした
    [drive_pane.brd, drive_pane.dxf, driver.sch]
2022-11-11 位置合せピンを追加した
    [drive.dxf, driver.brd, driver.sch]
2022-11-11 ロゴを追加した。
    [drive.dxf, drive_pane.dxf, driver.brd]
2022-11-11 部品の数値を編集
    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
    [driver.brd, driver.sch]
2022-11-13 発注します
    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
    [drive_pane.brd, driver.brd, driver.sch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]
2022-11-13 発注したガーバーデータを追加した。
    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
2022-11-14 ステンシルデータを追加
    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
    [stencil.DXF]
2022-11-15 change README.MD
    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
2022-11-15 BOMの作成
    # 削除など: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
    [driver.csv]
2022-11-15 ゲート抵抗選定スクリプトの書き直し
    Pythonでグラフを書きながら検討した．1からコード書き直した．matplotlibのsubplotで電流と電圧のグラフを書き直した．理論が間違っているところがあったのでやり直し．
2022-11-15 ゲート抵抗選定スクリプトの書き直し
2022-11-17 some fix README.MD
    ブログ記事のリンク載せた
2022-12-04 next
    # 削除など: Remove
    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
    [drive.dxf, drive_pane.brd, drive_pane.dxf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]
2023-01-30 評価基板のアップデート
    [driver.brd, driver.sch]
2023-03-10 fix position BST condenser
    [drive.dxf, drive_pane.brd, drive_pane.dxf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]
2023-04-22 add SimpleFOC
    [driver.brd, driver.csv, driver_top_bom.csv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]
2023-04-22 create new program BLDC_programV2
2023-04-22 エンコーダ原点と角速度のコードを修正
2023-04-22 limitを設けた
2023-04-23 radianを使うように変更中
2023-04-23 モータドライバの故障診断プログラムを追加
2023-04-24 radianとdegreeの三角関数を作成
2023-04-24 強制転流SVPWMでモータが回るようになった
2023-04-25 PIDライブラリのエラーを修復
2023-04-25 abs,sqrt,atan2をMath.hに追加
2023-04-25 setPhaseVoltageにUdを追加，Diagnoseを変更中...
2023-04-25 センサードUqコントロールの検証(Diagnoseは一旦パス)
2023-04-25 速度PI制御に成功！！
2023-04-27 getTargetVelocityを追加
2023-05-01 シリアルで目標速度を送ると動くようになった
2023-05-03 ドレミファソラシド
2023-05-27 :sparkles: version1.2完成(基板発注)
    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
    [drive_pane.dxf, driver.brd, driver.sch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]
2023-06-13 v1.4 test
    # 削除など: Rem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
    [main.cpp]
2023-06-19 :sparkles: create V2.0 in KiCAD7
    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
    [BLDCDriver_V2.0.kicad_pcb, BLDCDriver_V2.0.kicad_sch]
2023-10-04 プログラム忘れたけど，途中まで
    # ファ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
    [main.c, main.h]
2023-10-04 :sparkles: V1.4 JLCPCBのPCBA検証用基板の設計DONE
    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
    [BLDCDriver_V2.0.kicad_pcb, BLDCDriver_V2.0.kicad_sch, drive.dxf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]
2023-11-23 PlatformIO + Serial + V1.4でモータが動くことを確認した
2023-12-14 基板生やした
    [BLDCDriver_1.5_KiCad.kicad_pcb, BLDCDriver_1.5_KiCad.kicad_sch]
2023-12-14 おそらくこれで速度司令を受けることができるようになった(未検証)
    0. ヘッダを受信
    1. vel[0]の 1byte目を受信
    2. vel[0]の 2byte目を受信
    3. vel[1]の 1byte目を受信
    4. vel[1]の 2byte目を受信
    5. vel[2]の 1byte目を受信
    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
2023-12-26 unionだった
2023-12-27 ✨受信プログラムを修正！！
    手動でシリアル送るとうまく行くけど、Pythonで送るやつは上手く行ってない
2024-01-05 :sparkles: 無理やりフラッシュに書き込み読み出しができることが確認取れたが電源を切るとリセットされる
    リンカスクリプトを編集していないので。プログラムメモリと衝突していないのがラッキーぐらいの感覚で、危ないのでやめたほうがいい。一応成功しており、プログラムを書き換えてもデータを保持しているので成功している。
    EEPROMが乗らないのでFLASHに磁気エンコーダの値を書き込もうとしている。1万回程度で壊れるらしいが、書き込み回数より先にMDが壊れるだろうと思っている。
2024-01-06 ✨CubeMXでプロジェクト生成して、FLASH書き込み読み出しができたのと、AS5048Aを読み取れた
    - stm32pioでPlatformIOのプロジェクトに変更している
    - HAL_SPI_TransmitReceive_DMAで0xFFFFに投げて、その次に空データ送りつけて読み込みをDMAでやっている
    - DMA、めっちゃ複雑なんかと思ったけど、CubeMXでの設定はめっちゃ簡単だった。DMAと普通のやつの違いがよくわからん。DMAを使うとリングバッファ的なやつを作れるのかな。今回そんなことしてないけど。
    - DMAで16bit送るようにしているっぽい。できているのだろう。
    - AS5048Aを12bitと勘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
2024-01-08 ✨PWM出力できた
    TIM1とTIM3を使って出力できた。1つのマイコンでBLDCを2つ回せるかも。
2024-01-08 ✨AS5048A読み取り部の抽象化をした
    getAngleDegで読めてない時に1440でエラーがわかるようになっている。
2024-01-11 ✨SerialをDMAで受信できた
    この後memsetなどを使ってfifoを実装する。
2024-01-11 ✨Serial Wrapperを書いた
    - 受信はDMAで
    - 送信は普通の送信
2024-01-11 ✨データ送信プロトコルでちゃんと受信できた
    6. vel[2]の 2byte目を受信
    7. vel[3]の 1byte目を受信
    8. vel[3]の 2byte目を受信
    9. チェックサムを受信
    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
2024-01-11 ✨Serial,PWM,SPIを同時に宣言しても動いた
2024-01-11 ✨今のBLDCドライバようにプログラムを描き始めた
2024-01-11 ✨GPIOピンのラッパーが動いた
2024-01-12 ✨DigitalOutのoperator boolを追加
    led = !ledができるようになった。
2024-01-12 ✨DWTを用いた実行時間計測用Timerクラスの実装完了
2024-01-12 ✨SPIのCSピンのON/OFFを1msから10nsに変更して1ループ20KHzにできた
2024-01-13 ✨CANでデータフレーム送信できた
    https://hsdev.co.jp/stm32-can/
    hcan1.Instance = CAN1;
    hcan1.Init.Prescaler = 5;
    hcan1.Init.Mode = CAN_MODE_NORMAL;
    hcan1.Init.SyncJumpWidth = CAN_SJW_1TQ;
    hcan1.Init.TimeSeg1 = CAN_BS1_6TQ;
    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
2024-01-13 ✨CANの受信が確認できた
2024-01-13 🔥ゴミファイルを消した
2024-01-13 ✨CANのラッパー動いた
    受信割り込みでこの関数が呼び出されるので、オーバーロードする必要あり。
    void HAL_CAN_RxFifo0MsgPendingCallback(CAN_HandleTypeDef *hcan) {
    if (can.getHcan() == &hcan1) {
    can.recv(canRecvData);
    }
    }
2024-01-13 ✏️BLDCライブラリをIncludeしてコンパイルを通るようにした。
    次が処理の実装とかかな。
2024-01-14 ✨EagleでCANRDとCANTDを逆にした
    プロダクションできるはず
    [driver.brd, driver.sch]
2024-01-14 ✨MKS CANable2.0(slcan)を使ってPython-canで送受信できた
2024-01-15 ✨FloatのPrintfに対応したはず
2024-01-15 ✨printf floatできた
    asm(".global _printf_float");
2024-01-16 ✨STSPIN32G4で基板設計を始めた
    [BLDCDriver_1.5_KiCad.kicad_pcb, BLDCDriver_1.5_KiCad.kicad_sch, PowerOut.kicad_sch]

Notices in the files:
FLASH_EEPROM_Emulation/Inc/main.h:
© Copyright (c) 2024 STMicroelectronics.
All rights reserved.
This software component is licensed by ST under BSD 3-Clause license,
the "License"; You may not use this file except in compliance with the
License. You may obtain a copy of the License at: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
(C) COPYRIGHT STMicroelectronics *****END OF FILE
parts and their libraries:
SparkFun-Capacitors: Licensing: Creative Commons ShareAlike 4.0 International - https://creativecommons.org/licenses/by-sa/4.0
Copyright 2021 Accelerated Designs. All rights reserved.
